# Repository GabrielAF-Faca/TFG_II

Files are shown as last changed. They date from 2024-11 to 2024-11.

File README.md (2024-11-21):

# Robô Quadrúpede Com 3 DOF Por Perna

## Vídeos do funcionamento
https://www.youtube.com/playlist?list=PLtiqwHhrwyDy4FeO3HXZ96Ta0Fswptasy

## Componentes
Raspberry Pi Pico W <br>
12x Servomotores MG90S <br>
Conversor Step-Down <br>
Resistor 1k ohm <br>
Resistor 2k ohm <br>
Bateria Li-Ion 2s (7.4v) 2500 mAh <br>

## Circuito
Diagrama de circuito com as conexões dos componentes
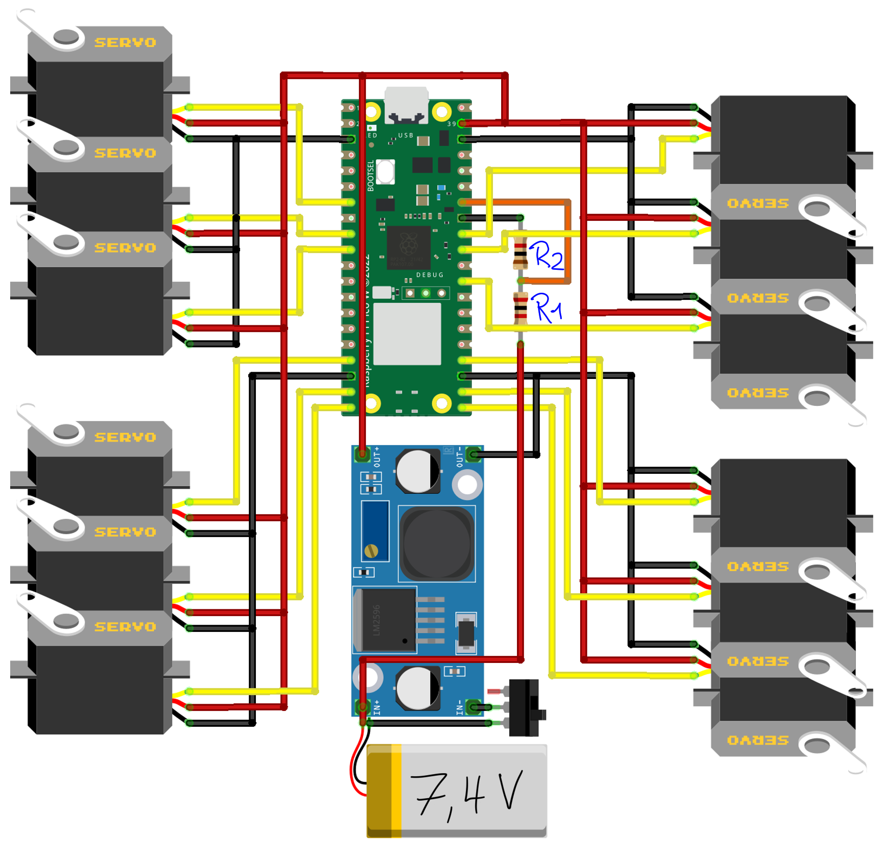
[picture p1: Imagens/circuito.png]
Circuito


R1 = 2R2 | Neste caso, R1 = 2k ohm e R2 = 1k ohm 

Soldar em uma perfboard
protoboard
(A) Raspberry Removido; (B) Raspberry Adicionado

## Montagem
Imprimir modelos 3D da pasta Modelos_3d

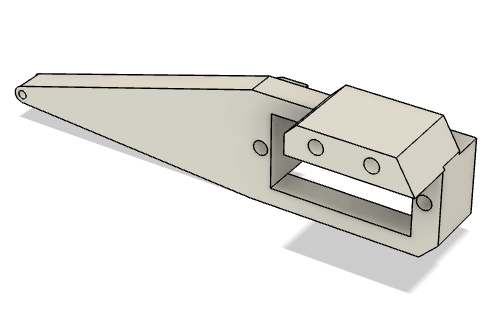
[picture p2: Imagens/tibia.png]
Tibia


Encaixar cabeçotes dos servos  
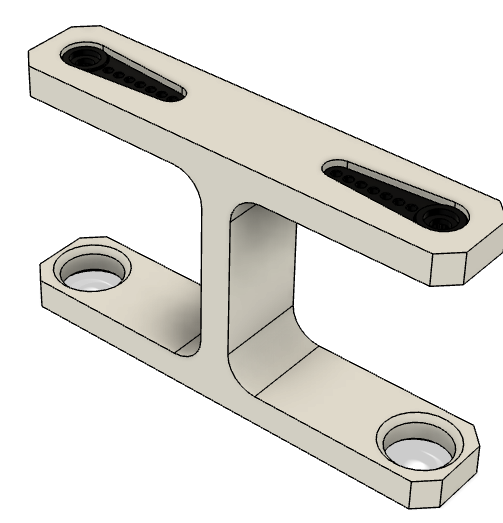
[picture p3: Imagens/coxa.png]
Montagem dos servomotores na coxa


Encaixar servomotores e parafusar (4x)<br>
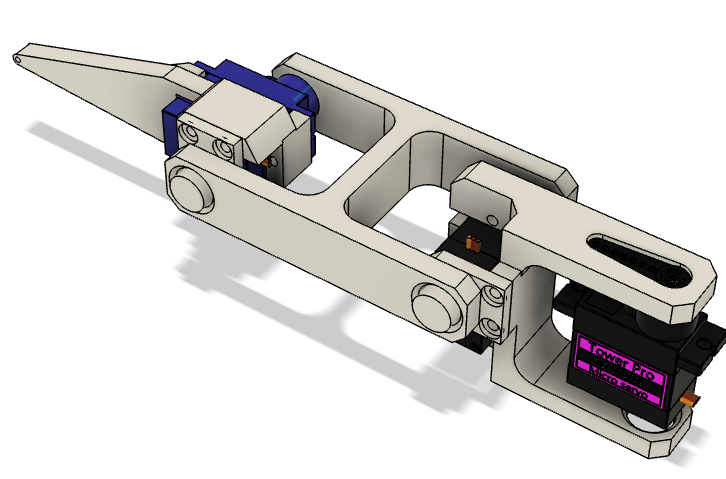
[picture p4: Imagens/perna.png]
Perna


Encaixar Pernas nas bases e parafusar
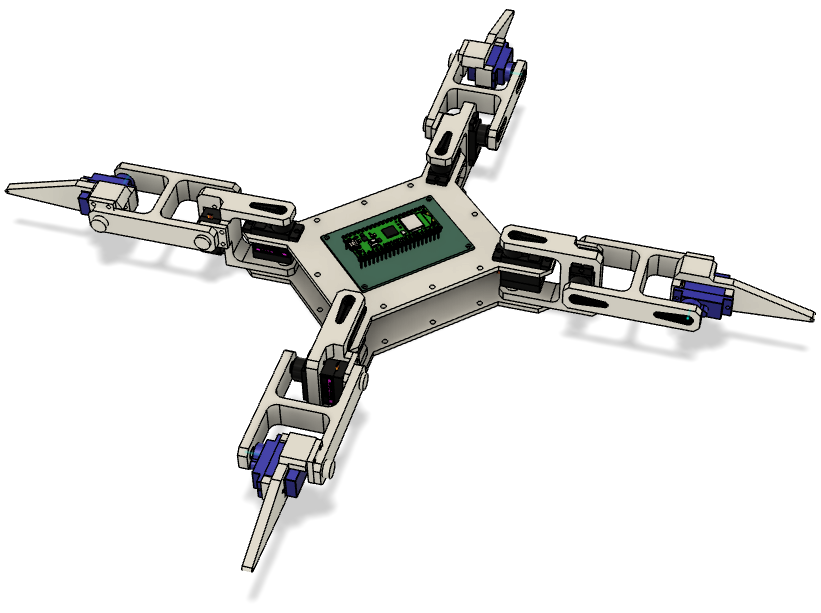
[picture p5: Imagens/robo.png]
Robo


Conectar todos os motores e bateria
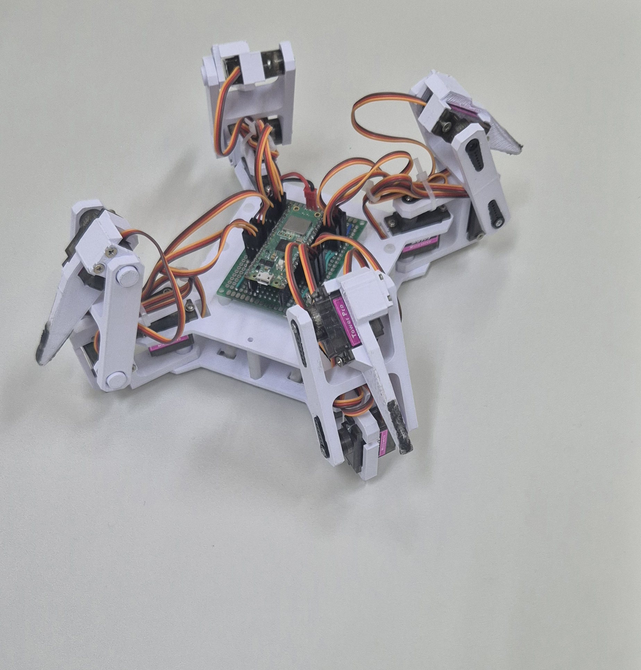
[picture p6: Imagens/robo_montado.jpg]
Robo Montado


## Programação
Conectar Raspberry no computador através de cabo usb <br>
Abrir o Thonny IDE <br>

Selecionar porta do Raspberry no canto inferior direito <br>
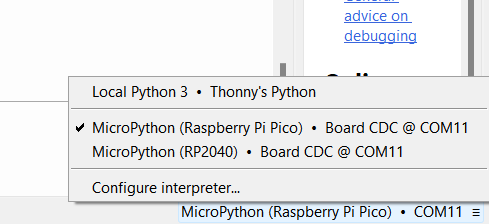
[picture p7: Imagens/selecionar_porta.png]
selecionar


Fazer Upload dos arquivos para o Raspberry <br>
Executar código <br>
Conectar na rede Wi-Fi do robô (através de smartphone)<br>
wifi

Acessar o endereço 192.168.4.1 no browser web (através de smartphone)<br>

Controlar robô

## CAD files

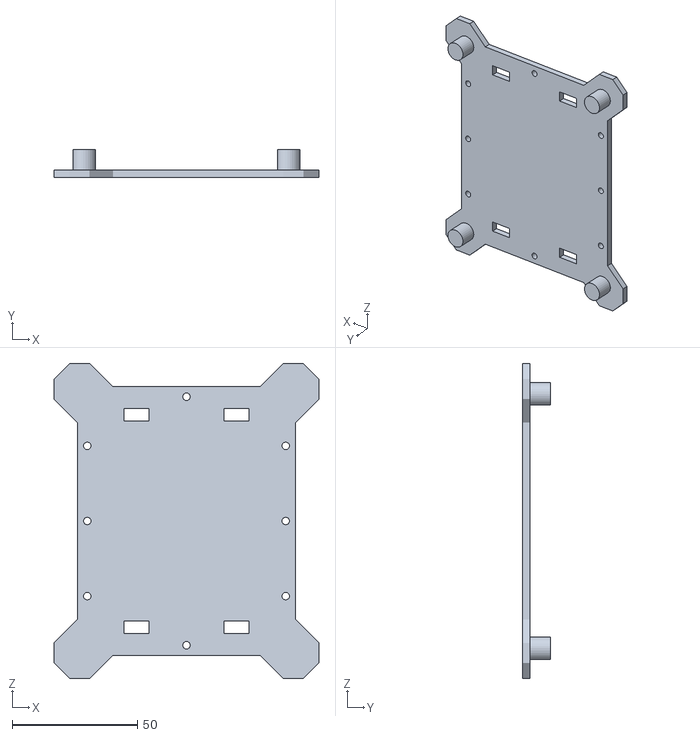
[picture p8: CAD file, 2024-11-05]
Modelos_3d/Corpo Inferior.stl
105.9 x 11.3 x 125.9

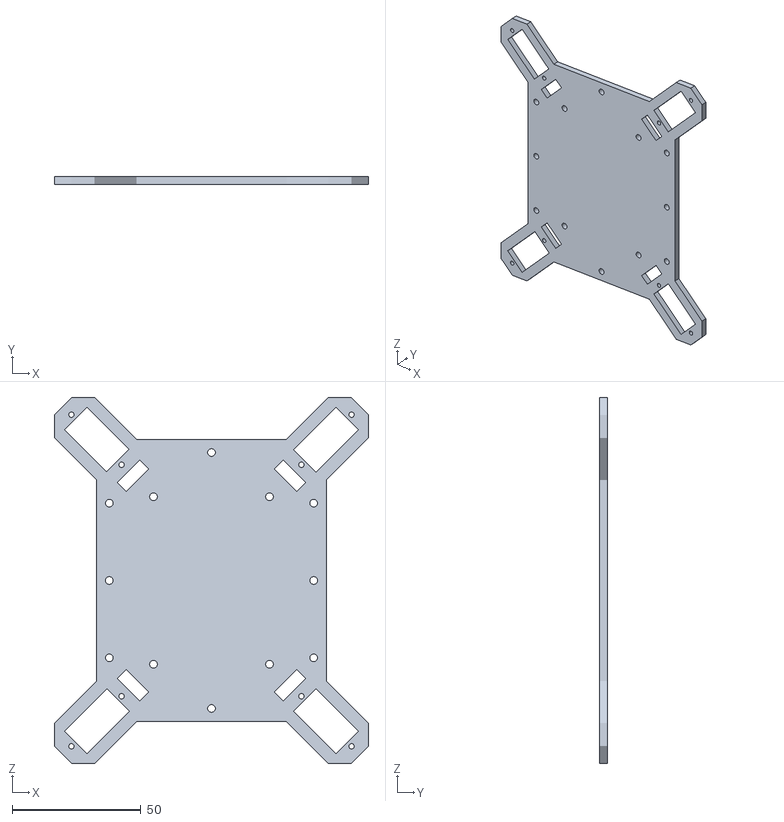
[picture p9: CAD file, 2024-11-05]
Modelos_3d/Corpo Superior.stl
122.0 x 3.00 x 142.0

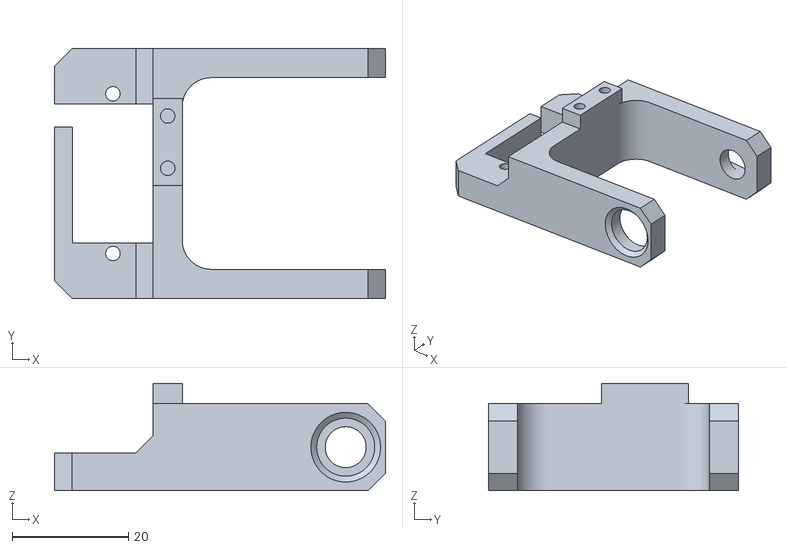
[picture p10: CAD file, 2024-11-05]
Modelos_3d/Junta Inicio Perna.stl
57.0 x 43.0 x 18.5

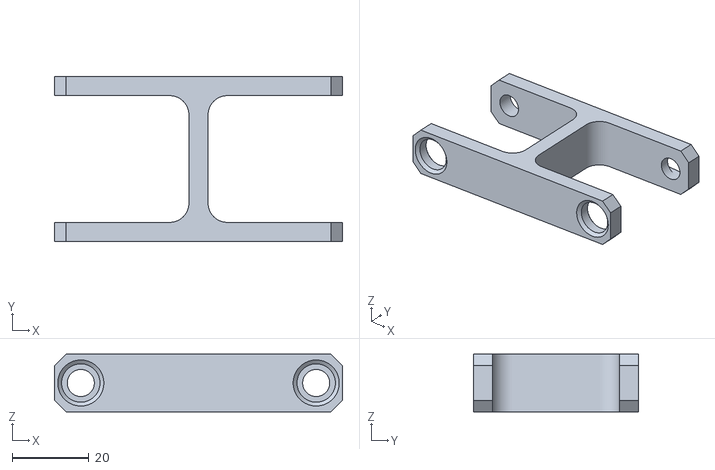
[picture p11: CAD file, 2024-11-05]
Modelos_3d/Coxa.stl
75.0 x 43.0 x 15.0

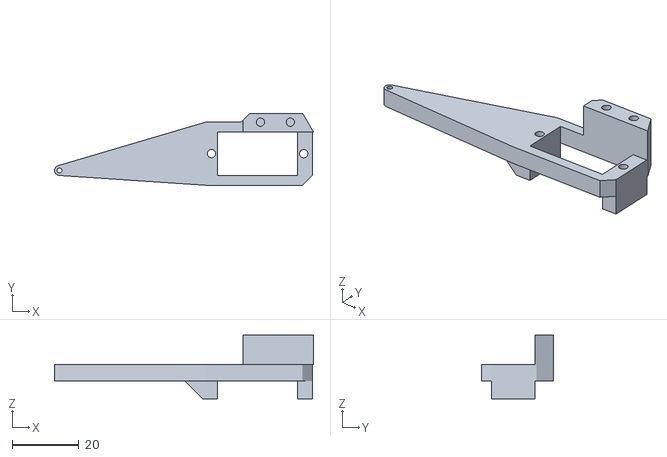
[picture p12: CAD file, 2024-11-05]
Modelos_3d/Tibia.stl
77.8 x 21.5 x 19.2

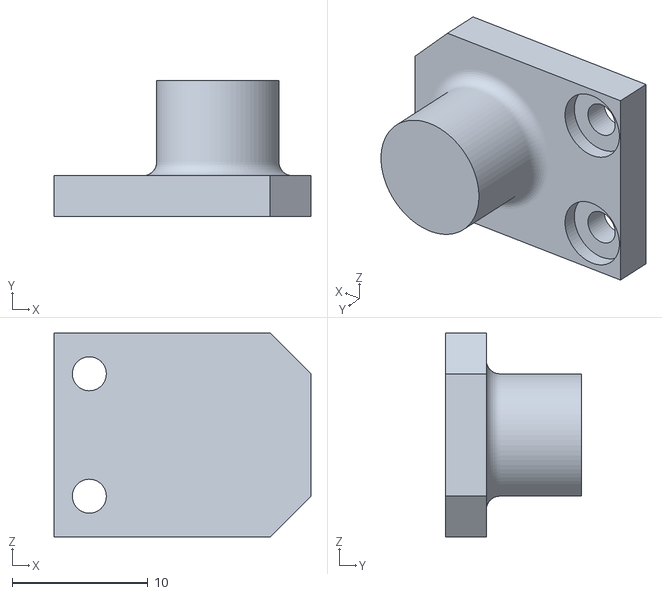
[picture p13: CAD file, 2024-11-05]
Modelos_3d/Encaixe.stl
18.9 x 10.0 x 15.0

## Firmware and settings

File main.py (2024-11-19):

from machine import ADC 
from picozero import pico_led
from robo import Robo
from time import sleep

import machine
import math
import network
import socket
import utime

gravando = False 
divisor_tensao = machine.ADC(28)


def read_battery():
    adc_reading  = divisor_tensao.read_u16()
    adc_voltage = (adc_reading - 35467) / (51231 - 35467)
    battery = adc_voltage*10
    print(battery)
    return math.floor(battery), battery*10


def webpage(ligado, grav):
    
    if ligado:
        cor_ligar = 'green'
        cor_hover = 'rgb(0, 93, 0)'
        disabled = ''
    else:
        cor_ligar = 'red'
        cor_hover = 'rgb(181, 0, 0)'
        disabled = 'disabled'
        
    html = ""
    
    with open("./index.html") as file:
        html = file.read()
    
    bateria_string = ""
    
    bateria = read_battery()
        
    print(bateria)
    
    bateria = read_battery()[0]
    
    for i in range(bateria):
        bateria_string += "<span>&#128994</span>"
    
    for i in range(10-bateria):
        bateria_string += "<span>&#128308</span>"
    
    html = html.replace("#DISABLED#", '#DISABLED#' + disabled)
    html = html.replace("#COR_BOTAO_LIGAR#", cor_ligar)
    html = html.replace("#COR_BOTAO_HOVER#", cor_hover)
    html = html.replace("#INDICADOR_BATERIA#", bateria_string)
    
    if grav:
        html = html.replace("#BOTAO_GRAVAR#", "Parar")
    else:
        html = html.replace("#BOTAO_GRAVAR#", "Iniciar")
     
    return str(html)
    #return u"".join(html).encode("utf-8")
        
def ap_mode(ssid, password):
    global gravando
    # Just making our internet connection
    ap = network.WLAN(network.AP_IF)
    ap.config(essid=ssid, password=password)
    ap.active(True)

    while ap.active() == False:
        pico_led.toggle()
        pass
    print('AP Mode Is Active, You can Now Connect')
    print('IP Address To Connect to:: ' + ap.ifconfig()[0])

    s = socket.socket(socket.AF_INET, socket.SOCK_STREAM)   #creating socket object
    s.bind(('', 80))
    s.listen(5)
    
    robo = None
    
    momento_inicio = 0
    momento_final = 0
    bateria_inicio = 0
    bateria_final = 0
    trajeto_analise = ""
    distancia = 0
    
    while True:
        conn, addr = s.accept()
        print('Got a connection from %s' % str(addr))
        pico_led.on()
        request = conn.recv(1024)
        print('Content = %s' % str(request))
        try:
            request = request.split()[1]
        except IndexError:
            pass
        if request.startswith('/ligar?'):
            if robo == None:
                robo = Robo()
            else:
                robo.perna1.posicao_off()
                robo.perna2.posicao_off()
                robo.perna3.posicao_off()
                robo.perna4.posicao_off()
                del robo
                robo = None
        elif request.startswith('/levantar'):
            robo.levantar()
        elif request.startswith('/dancar?'):
            robo.dancar()
        elif request.startswith('/frente'):
            robo.frente()
        elif request.startswith('/deitar'):
            robo.abaixar()
        elif request.startswith('/esquerda'):
            robo.esquerda()
        elif request.startswith('/direita'):
            robo.direita()
        elif request.startswith('/tras'):
            robo.tras()
        elif request.startswith('/girarEsq'):
            robo.gira_esquerda()
        elif request.startswith('/girarDir'):
            robo.gira_direita()
        elif request.startswith('/trajeto'):
            tipo_trajeto = str(request).split("?trajeto=")[1].rstrip("'")
            #print(tipo_trajeto)
            
            if not gravando:
                gravando = True
                trajeto_analise = tipo_trajeto
                momento_inicio = utime.ticks_ms()
                bateria_inicio = read_battery()[1]
            else:
                gravando = False
                with open('./trajetos.csv', 'a') as file:
                    momento_final = utime.ticks_ms() - momento_inicio
                    bateria_final = read_battery()[1]
                    distancia = tipo_trajeto
                    
                    file.write(f"{trajeto_analise}, {distancia}, {momento_final}, {bateria_inicio}, {bateria_final}\n")
            
        #print(request)
        
        response = webpage(robo != None, gravando)
        conn.send(response)
        conn.close()


ssid = 'Robo_Aranha'
password = '12345678'

ap_mode(ssid, password)


#robo.dancar()
#robo.perna1.move_to_point(90, -15, 10)
#robo.testar_perna()

#for i in range(10):
#    robo.andar()

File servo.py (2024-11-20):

from machine import Pin, PWM

class Servo:
 
    def __init__(self, pin: int or Pin or PWM, freq=50, minVal=2500, maxVal=7500, reverse=False):

        if isinstance(pin, int):
            pin = Pin(pin, Pin.OUT)
            
        if isinstance(pin, Pin):
            self.__pwm = PWM(pin)
            
        if isinstance(pin, PWM):
            self.__pwm = pin
            
        self.__pwm.freq(freq)
        self.minVal = minVal
        self.maxVal = maxVal
        
        self.reverse = reverse
        
        self.angle = None
        
    def read(self):
        return self.angle
    
    def write(self, angle):
          
        if self.reverse:
            angle = 180 - angle
        
        if angle <= 0:
            angle = 1
            
        if angle > 180:
            angle = 180
        
        self.angle = angle
        
        value = (angle) * (1024) / (180)
        
        self.goto(round(value)) # Convert range value to angle value
        
        return angle
    
    def goto(self, value: int):

        if value < 0:
            value = 0
            
        elif value > 1024:
            value = 1024
            
        delta = self.maxVal - self.minVal
        
        target = int(self.minVal + ((value / 1024) * delta))
        
        self.__pwm.duty_u16(target)
        
        
    def min_pos(self):
        self.__pwm.duty_u16(self.minVal)
    
    def max_pos(self):
        self.__pwm.duty_u16(self.maxVal)
    
 

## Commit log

2024-11-21 Rename Captura de tela 2024-11-21 151110.png to Junta Inicio Perna.png
2024-11-21 Rename Captura de tela 2024-11-21 152055.png to robo.png
2024-11-21 Rename Captura de tela 2024-11-21 151143.png to tibia.png
2024-11-21 Rename Captura de tela 2024-11-21 151944.png to perna.png
